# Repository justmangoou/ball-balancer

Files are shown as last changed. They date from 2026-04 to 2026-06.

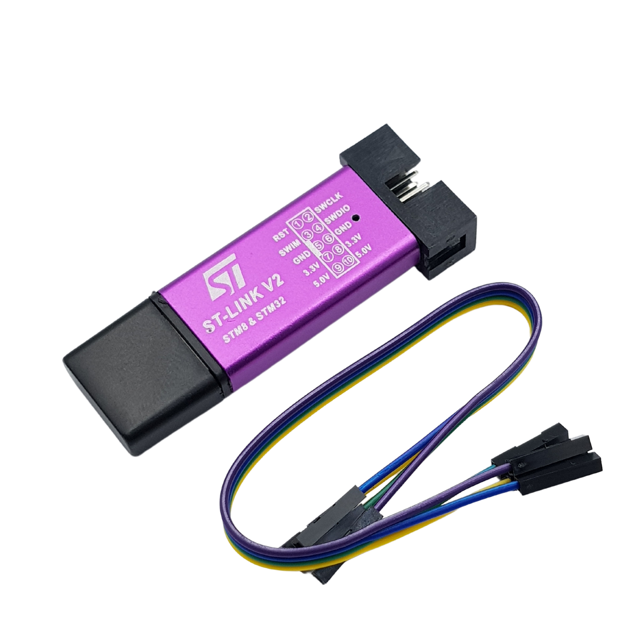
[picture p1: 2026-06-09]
report/assets/st-link.png

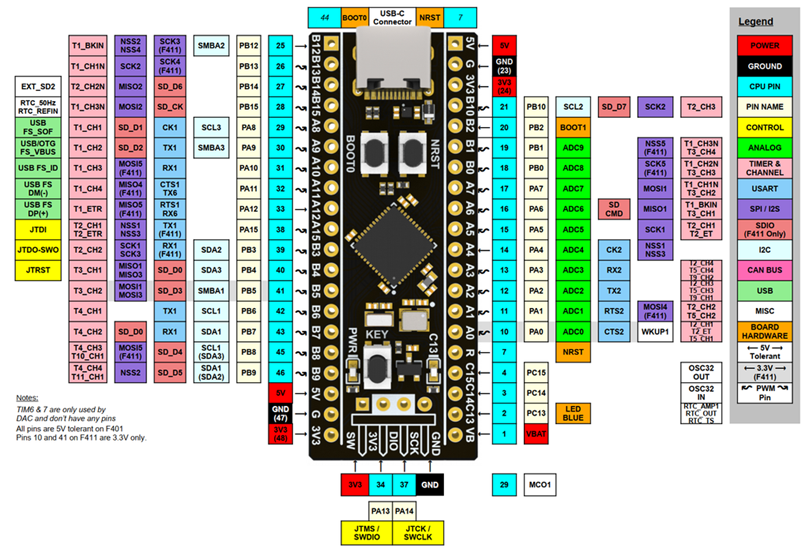
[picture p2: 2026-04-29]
report/assets/STM32F411CEU6-pinout.png

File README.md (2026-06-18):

# Ball Balancer

## Acknowledgements & Credits

This project is heavily inspired by and built upon the open-source work of **Aaed Musa** ([Ball Balancer on Instructables](https://www.instructables.com/Ball-Balancer/)). 

Python scripts to log data and graph visualizer are generated using Claude Sonnet 4.6.

## Major changes (compare to original work)
- Use STM32F4 "Blackpill" instead of Teensy 4.1.
- Use STM32 firmware development tools instead of Arduino (using Hardware timer, FPU, ...).
- Re-design R-joint so it does not slip (mismatch step when working).

## Development
### Pre-requisites
- Python 3.10 or higher (with `matplotlib`, `numpy` and `pyserial` libraries)
- STM32CubeMX
- STM32CubeCLT
- OpenOCD
- Clion (preferred)
- ST-Link V2

*It's also possible to use STM32CubeIDE, but CLion is recommended for better coding and debugging experience.*

### Firmware
All firmware code is located in the `firmware` directory. The project is configured for STM32F411CEU6 "Blackpill" microcontroller.

## Scipts
To log data to terminal only:
```bash
python loggger.py
```

To log data to terminal, draw graph ``x_err``, ``y_err``, ``x_out``, ``y_out`` and save to csv file:
```bash
python live_debugger.py
```

To see the graph of the logged data from csv file:
```bash
python log_viewer.py --file logs/xxxx-xx-xx_xx-xx-xx.csv
```

## PID Tuning Tracker
| Times | Time | Kp | Ki | Kd | 
| :---: | :---: | :---: | :---: | :---: |
| **1** | [2026-06-09_14-49-30](logs/2026-06-09_14-49-30.csv) | `6E-4f` | `6E-5f` | `10E-6f` |
| **2** | [2026-06-09_16-08-42](logs/2026-06-09_16-08-42.csv) | `1.3E-3f` | `7E-5f` | `2.3E-5f` |
| **3** | [2026-06-09_16-36-50](logs/2026-06-09_16-36-50.csv) | `1.1E-3f` | `5E-5f` | `2.3E-5f` |
| **4** | [2026-06-09_16-38-50](logs/2026-06-09_16-38-50.csv) | `1.1E-3f` | `5E-5f` (x) / `7E-5f` (y) | `2.3E-5f` |
| **5** | [2026-06-09_16-54-01](logs/2026-06-09_16-54-01.csv) | `1.1E-3f` | `5.5E-5f` (x) / `7.5E-5f` (y) | `2.3E-5f` |
| **6** | [2026-06-09_16-58-05](logs/2026-06-09_16-58-05.csv) | `1.1E-3f` | `6E-5f` (x) / `7.5E-5f` (y) | `2.3E-5f` |

### BOM
| ID | Name  | Quantity | Description |
| --- | --- | --- | --- |
| STM32F411CEU6 | STM32 BlackPill | 1 | Microcontroller |
|  | Resistive Touch Panel | 1 | 4 Pins  |
| 17HS4401S | Stepper 42x42mm | 3 | 1.5 - 2A |
| TMC2208 | Stepper Driver | 3 |  |
| LM2596 | Voltage Regulator | 1 | 4 - 35 VDC Input, 1 - 35 VDC Ouput (3A)  |
|  | Capacitor | 3 | 35V - 220uF |
|  | 24V power supply  | 1 | 24V - 5A |
|  | Terminal Connector | 1 | 15A - 12 Ports |
|  | FPC/FFC to DIP Adapter Board | 1 | 4 Pins |
|  | DC Jack | 1 |  |
|  | USB to TTL | 1 | |
|  | Male and female header pin | many |  |

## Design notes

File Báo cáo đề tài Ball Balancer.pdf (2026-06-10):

### ĐẠI HỌC QUỐC GIA HÀ NỘI

### TRƯỜNG ĐẠI HỌC CÔNG NGHỆ

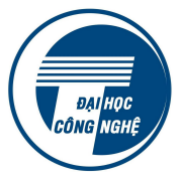
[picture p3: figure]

### BÁO CÁO MÔN HỌC

### THỰC HÀNH VÀ XÂY DỰNG ROBOT 2

### Đề tài: Robot cân bằng bóng trên mặt phẳng

Giảng viên hướng dẫn: | Đặng Anh Việt Nguyễn Quốc Bảo
Sinh viên thực hiện: | Nguyễn Hoàng Tuấn - 24022923 Đỗ Minh - 24022889
Lớp: | K69E-RE1
Lớp học phần | RBE2022 2

Hà Nội — 2026

## Mục lục

## Danh mục hình

Hình 3.8 Sơ đồ kết nối tổng thể giữa vi điều khiển, driver động cơ và các khối chức

Hình 5.1 Đồ thị biểu diễn sự thay đổi về đầu vào/ra của hai trục X/Y

Hình 5.2 Đồ thị biểu diễn sự thay đổi về đầu vào/ra của hai trục X/Y

## Danh mục bảng

Bảng 3.8 Sơ đồ kết nối các chân của driver TMC2208 với nguồn và động cơ bước . 20

## Danh mục ký hiệu và từ viết tắt

ADC | Analog-to-Digital Converter Bộ chuyển đổi tín hiệu tương tự sang tín hiệu số.
ARM | Advanced RISC Machine Kiến trúc vi xử lý dựa trên tập lệnh rút gọn (RISC).
DC | Direct Current Dòng điện một chiều.
DIP | Dual In-line Package (hoặc Dual In-line Pins) Kiểu chân linh kiện có hai hàng chân song song, khoảng cách tiêu chuẩn (thường là 2.54mm).
DWT | Data Watchpoint and Trace Khối ngoại vi thuộc lõi ARM hỗ trợ giám sát hệ thống và cung cấp bộ đếm chu kỳ xung nhịp.
FFC | Flexible Flat Cable Cáp dẹt mềm, dùng để kết nối dẫn điện giữa các bo mạch hoặc module thông qua đầu cắm chuyên dụng.
FPC | Flexible Printed Circuit Mạch in dẻo, có thể tích hợp linh kiện và đường mạch phức tạp trên nền vật liệu đàn hồi, dùng cho các kết nối nhỏ gọn.
FPU | Floating Point Unit Bộ xử lý số học dấu chấm động.
GPIO | General Purpose Input/Output Các chân vào/ra đa dụng của vi điều khiển.
IDE | Integrated Development Environment Môi trường phát triển tích hợp dùng để viết, biên dịch và quản lý mã nguồn.

NEMA | National Electrical Manufacturers Association Chuẩn kích thước mặt bích động cơ (ví dụ NEMA 17).
PID | Proportional–Integral–Derivative Thuật toán điều khiển phản hồi gồm ba thành phần Tỉ lệ (P), Tích phân (I) và Đạo hàm (D).
PWM | Pulse Width Modulation Kỹ thuật điều chế độ rộng xung dùng để kiểm soát mức cống suất trung bình.
RMS | Root Mean Square Giá trị hiệu dụng của tín hiệu (ví dụ điện áp/dòng), tương đương giá trị DC tạo ra cùng công suất trên tải.
ROM | Read-Only Memory Bộ nhớ chỉ đọc, dùng để lưu trữ chương trình.
RPS | Revolute–Prismatic–Spherical Chuỗi khớp quay–tịnh tiến–cầu trong cơ cấu robot song song.
SRAM | Static Random Access Memory Bộ nhớ truy cập ngẫu nhiên tĩnh, dùng để lưu dữ liệu tạm thời khi chạy chương trình.
SYSCLK | System clock Xung nhịp hệ thống của vi điều khiển.
TIM | Timer Bộ định thời: tạo mốc thời gian và xung nhịp để đếm, tạo ngắt định kỳ, đo độ rộng/tần số xung và tạo PWM.
UART | Universal Asynchronous Receiver/Transmitter Chuẩn truyền nhận dữ liệu nối tiếp bất đồng bộ.

## CHƯƠNG 1: GIỚI THIỆU

### 1.1. Bài toán

Hệ thống cân bằng bóng trên mặt phẳng là một bài toán điển hình trong lĩnh vực

điều khiển tự động, thường được dùng để minh họa điều khiển phản hồi và khả năng ổn

định của một hệ cơ điện tử.

Đây là một bài toán thách thức do hệ có nhiều yếu tố phi tuyến và không lý tưởng.

Chuyển động của bóng phụ thuộc vào góc nghiêng của mặt phẳng, ma sát và đặc tính bề

mặt. Ngoài ra, hệ chịu ảnh hưởng của độ trễ và nhiễu phát sinh từ phần cơ khí cũng như

từ quá trình đo lường. Những yếu tố này khiến hệ có xu hướng xuất hiện dao động hoặc

không đáp ứng được yêu cầu về biên độ và tốc độ nếu hệ thống không được thiết kế và

hiệu chỉnh phù hợp.

### 1.2. Mục tiêu và phạm vi của đề tài

Mục tiêu của đề tài là xây dựng một hệ thống có khả năng:

- Xác định vị trí quả bóng trên mặt phẳng: thu nhận và xử lý tín hiệu để xác

định tọa độ (x, y) của bóng.

- Điều khiển mặt phẳng để đưa bóng về vị trí đặt: xây dựng thuật toán điều

khiển nhằm điều chỉnh chuyển động của mặt phẳng để giảm sai lệch vị trí.

- Duy trì trạng thái cân bằng ổn định: hạn chế dao động, nhiễu và đảm bảo sai

số xác lập nhỏ quanh vị trí mong muốn.

Trong phạm vi đề tài, hệ thống được triển khai trong môi trường thí nghiệm với một

quả bi thép đơn và mặt phẳng kích thước cố định. Bài toán tập trung vào điều khiển vị

trí trong một vùng làm việc giới hạn trên mặt phẳng và đánh giá chất lượng điều khiển

thông qua các tiêu chí như: thời gian đáp ứng, độ dao động và sai số xác lập.

### 1.3. Cơ sở tham khảo

Đề tài tham khảo mô hình Ball Balancer của Aaed Musa được đăng trên nền tảng

Instructables: https://www.instructables.com/Ball-Balancer/.

Trong đề tài này, thiết kế cơ khí được kế thừa với kích thước và tỉ lệ được điều

chỉnh phù hợp với phần cứng. Sơ đồ kết nối mạch được dựa trên nguyên lý tương tự, với

một số thay đổi nhằm đảm bảo sự tương thích với linh kiện được sử dụng.

## CHƯƠNG 2: CƠ SỞ LÝ THUYẾT

### 2.1. Mô hình Robot 3-RPS

Robot 3RPS là một cơ cấu song song gồm 3 chân (3 nhánh) có chuỗi khớp theo thứ

tự: R (Revolute – khớp quay) ở đế, P (Prismatic – khớp tịnh tiến, thường là cơ cấu vít

me/đai ốc hoặc thanh trượt được dẫn động) và S (Spherical – khớp cầu) nối với bàn công

tác. Nhờ cấu trúc song song, 3RPS có độ cứng vững tốt, sai số tích lũy nhỏ và phù hợp

cho các bài toán điều khiển nghiêng mặt phẳng (tilt) như cân bằng bi.

Về bậc tự do, với bố trí đối xứng thường gặp, 3RPS tạo ra 3 bậc tự do của bàn công

tác (thường là 2 góc nghiêng roll/pitch và 1 tịnh tiến theo trục z). Khi điều khiển cân

bằng bi trên mặt phẳng, ta chủ yếu quan tâm đến hai góc nghiêng của bàn; còn độ cao z

thường được xem là hằng hoặc biến thiên nhỏ tùy theo thiết kế.

Để mô tả động học, đặt hệ tọa độ gốc {B} gắn với đế, hệ {P} gắn với bàn công tác.

Gọi Bi

là tọa độ các điểm gắn chân trên đế trong {B}, và Pi

là tọa độ các điểm gắn chân

trên bàn trong {P}, với i = 1..3. Tư thế của bàn được mô tả bởi ma trận quay R và vectơ

tịnh tiến p (từ {B} đến gốc {P}). Khi đó vectơ chân thứ i trong {B} là:

l

i = p + RPi − Bi

Chiều dài (hoặc hành trình hiệu dụng) của chân i là:

qi = ‖l
i

‖

Đây là dạng động học nghịch điển hình: cho tư thế mong muốn (R, p), ta tính được

q1

, q2

, q3

để sinh lệnh cho các cơ cấu tịnh tiến (xung bước/độ quay motor → dịch

chuyển). Ngược lại, động học thuận (từ qi
suy ra (R, p)) thường phức tạp hơn và hay được giải bằng phương pháp số; trong bài toán cân bằng, hệ thống có thể dùng cảm biến

(màn cảm ứng) để phản hồi trực tiếp trạng thái bi nên không nhất thiết phải giải động

học thuận chính xác ở mọi thời điểm.

### 2.2. Màn cảm ứng điện trở

Màn cảm ứng điện trở hoạt động dựa trên hai lớp dẫn điện được ngăn cách bởi một

lớp cách điện mỏng. Khi có lực tác động lên bề mặt, hai lớp này tiếp xúc tại điểm chạm,

tạo thành một cầu điện trở. Bằng cách đo điện áp tại điểm tiếp xúc, hệ thống có thể xác

định tọa độ theo hai trục X và Y.

Ưu điểm của loại màn này là chi phí thấp và có thể sử dụng với nhiều vật liệu tiếp

xúc. Tuy nhiên, nhược điểm là độ bền không cao, độ nhạy kém hơn so với màn cảm ứng

điện dung và không hỗ trợ đa điểm hiệu quả.

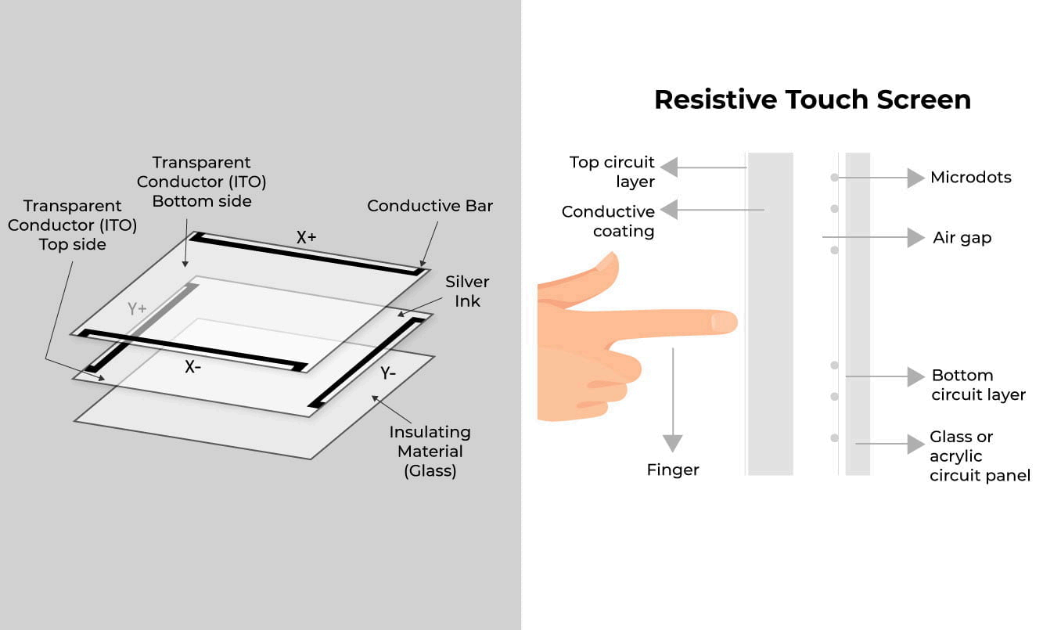
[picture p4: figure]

Hình 2.1: Cấu tạo của màn cảm ứng điện trở

### 2.3. Cơ sở phát xung động cơ bước

Động cơ bước được điều khiển thông qua hai tín hiệu STEP và DIR. Mỗi xung

STEP tương ứng với một bước dịch chuyển của động cơ, trong khi tín hiệu DIR xác định

chiều quay.

Trong hệ thống này, vận tốc được biểu diễn dưới dạng số thực và được tích lũy

theo từng chu kỳ timer. Khi giá trị tích lũy đạt ngưỡng xác định, hệ thống phát một xung

STEP và cập nhật vị trí hiện tại của động cơ. Phương pháp này cho phép điều khiển vận

tốc mượt mà trong khi vẫn duy trì chu kỳ timer cố định.

### 2.4. Thuật toán điều khiển PID

Thuật toán điều khiển Proportional–Integral–Derivative (PID) là một phương pháp

điều khiển phản hồi được sử dụng phổ biến trong các hệ thống. Trong đó tín hiệu điều

khiển được xác định dựa trên sai lệch giữa giá trị đặt và giá trị đo được của hệ thống. Cách

tiếp cận này cho phép hệ thống liên tục điều chỉnh để đạt được trạng thái mong muốn.

Bộ điều khiển PID bao gồm ba thành phần chính:

- Thành phần tỉ lệ (P): tạo ra tín hiệu điều khiển tỉ lệ với sai số tức thời, giúp hệ

thống phản ứng nhanh với sự thay đổi.

- Thành phần tích phân (I): tích lũy sai số theo thời gian, nhằm loại bỏ sai số xác

lập và cải thiện độ chính xác lâu dài.

- Thành phần đạo hàm (D): phản ánh tốc độ biến thiên của sai số, từ đó hỗ trợ

giảm dao động và cải thiện tính ổn định của hệ thống.

Biểu thức tổng quát của bộ điều khiển trong miền thời gian được viết như sau:

u(t) = Kp

e(t) + Ki ∫ e(t) dt + Kd

de(t)
dt

Trong đó:
- e(t) là sai lệch giữa giá trị mong muốn và giá trị đo được
- Kp

, Ki

, Kd

là các hệ số điều khiển.

Các tham số này cần được hiệu chỉnh phù hợp để đảm bảo hệ thống đạt được các đặc tính

đáp ứng mong muốn như thời gian xác lập ngắn, độ vượt quá nhỏ và sai số xác lập thấp.

Trong quá trình triển khai thực tế, hiện tượng integral windup có thể xảy ra khi

tín hiệu điều khiển bị giới hạn bởi các ràng buộc vật lý, trong khi thành phần tích phân

vẫn tiếp tục tích lũy sai số, dẫn đến đáp ứng vượt mức khi hệ thống trở lại vùng hoạt

động bình thường. Để khắc phục, có thể áp dụng một số kỹ thuật như giới hạn giá trị tích

phân (anti-windup clamping), tạm dừng tích lũy khi đầu ra bị bão hòa, hoặc hiệu chỉnh

lại thành phần tích phân dựa trên tín hiệu điều khiển thực tế.

## CHƯƠNG 3: THIẾT KẾ VÀ TRIỂN KHAI HỆ THỐNG

### 3.1. Thiết kế tổng thể

Hệ thống được thiết kế theo mô hình điều khiển vòng kín, trong đó vị trí của quả

bóng được đo liên tục và sử dụng làm tín hiệu phản hồi để điều chỉnh trạng thái của

hệ thống.

Về mặt chức năng, hệ thống bao gồm ba khối chính:

- Khối cảm biến: sử dụng màn hình cảm ứng điện trở để xác định tọa độ (x, y)

của quả bóng.
- Khối xử lý: vi điều khiển thực hiện nhiệm vụ thu nhận dữ liệu và tính toán tín

hiệu điều khiển.

- Khối chấp hành: bao gồm driver và các động cơ bước để điều chỉnh góc nghiêng

của mặt phẳng.

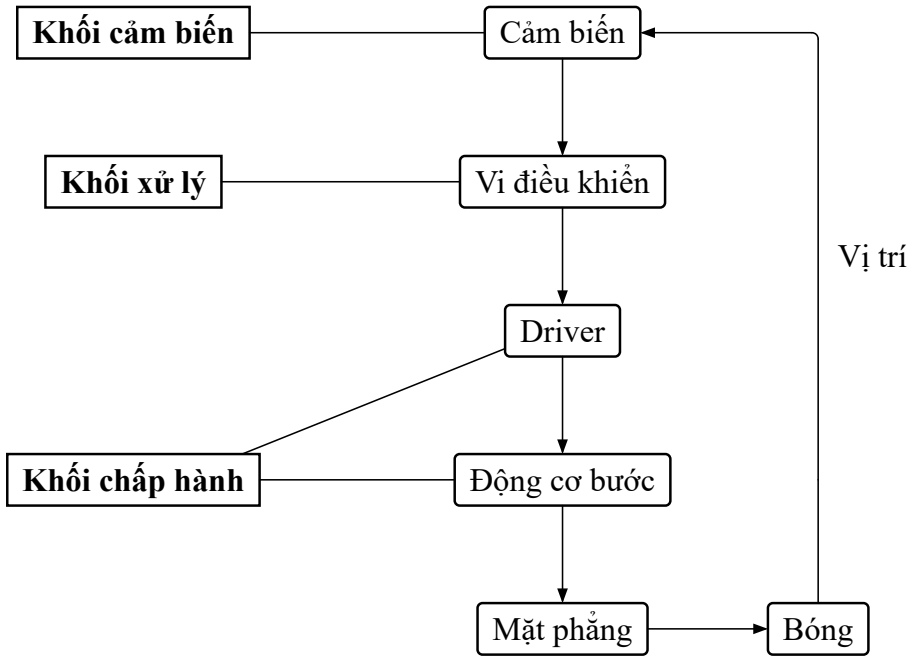
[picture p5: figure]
Vị trí; Cảm biến; Vi điều khiển; Driver; Động cơ bước; Mặt phẳng; Bóng; Khối cảm biến; Khối xử lý; Khối chấp hành

Hình 3.1: Sơ đồ khối tổng thể của hệ thống

Nguyên lý hoạt động của hệ thống như sau: tín hiệu vị trí từ cảm biến được đưa về bộ

điều khiển để xác định sai lệch so với vị trí đặt. Tín hiệu điều khiển sau đó được gửi tới

các động cơ bước nhằm điều chỉnh góc nghiêng của mặt phẳng, từ đó chi phối chuyển

động của quả bóng. Quá trình này được lặp lại liên tục theo thời gian thực để đảm bảo

hệ thống duy trì trạng thái cân bằng ổn định.

### 3.2. Thiết kế phần cứng

### 3.2.1. Danh sách linh kiện

### 3.2.1.1. Vi điều khiển STM32F411CEU6

STM32F411CEU6 (Blackpill) là vi điều khiển thuộc dòng STM32F4 của STMi-

croelectronics, sử dụng nhân ARM Cortex-M4 tích hợp Floating Point Unit (FPU), cho phép xử lý hiệu quả các phép toán số thực, phù hợp với các hệ thống điều khiển yêu cầu

hiệu suất cao.

Bảng 3.1: Thông số kỹ thuật STM32F411CEU6

Nhân | ARM 32-bit Cortex-M4
Tốc độ xung nhịp tối đa | 100 MHz
Bộ nhớ Flash (ROM) | 512 KB
Bộ nhớ SRAM | 128 KB
GPIO | 34 chân I/O
ADC | 12-bit, 9 kênh
Kích thước | 21 x 53 mm

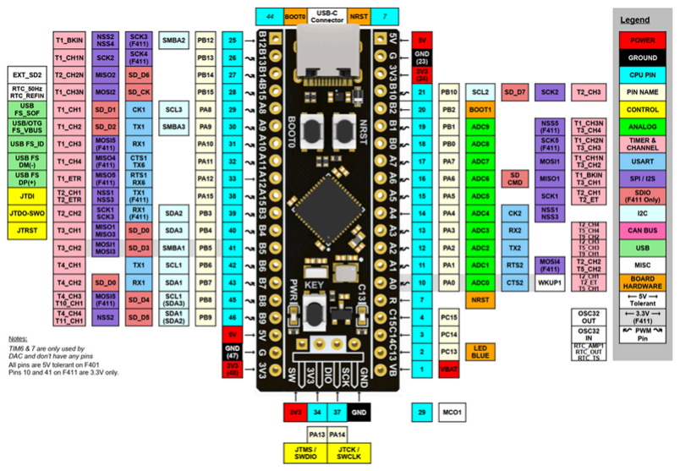
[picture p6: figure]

Hình 3.2: Sơ đồ chân của STM32F411CEU6 (Blackpill)

### 3.2.1.2. Màn cảm ứng điện trở

Màn hình cảm ứng điện trở được sử dụng để thu nhận thông tin vị trí tiếp xúc

trên bề mặt. Với cấu trúc 4 dây điện trở, thiết bị có khả năng xác định vị trí chạm với

độ chính xác tương đối cao và ổn định. Nhờ kích thước vùng hoạt động lớn và cấu tạo

đơn giản, loại màn hình này phù hợp với các ứng dụng yêu cầu xác định vị trí trên mặt

phẳng với chi phí thấp. Nguyên lý hoạt động được trình bày tại Mục 2.2.

Bảng 3.2: Thông số kỹ thuật màn cảm ứng điện trở

Kích thước | 9 inch
Vùng hoạt động | 210 × 126 mm
Vật liệu bề mặt | Màng phim + kính

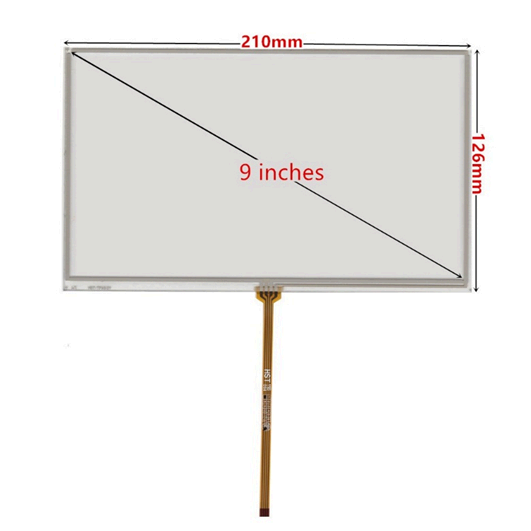
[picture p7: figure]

Hình 3.3: Màn hình cảm ứng điện trở 9″

### 3.2.1.3. Driver TMC2208

Driver TMC2208 là bộ điều khiển động cơ bước tích hợp các công nghệ

StealthChop2™︎ và SpreadCycle™︎ của Trinamic. Các công nghệ này giúp hạn chế tiếng

ồn, đồng thời đảm bảo chuyển động mượt với độ chính xác cao thông qua cơ chế vi

bước. Đồng thời, driver tối ưu hiệu suất năng lượng và giảm sinh nhiệt trong quá trình

vận hành lâu dài. Dòng điện cấp cho động cơ có thể được điều chỉnh thông qua điện áp

tham chiếu (Vref) hoặc giao tiếp UART, cho phép tự cấu hình tùy theo yêu cầu hệ thống.

Bảng 3.3: Thông số kỹ thuật driver TMC2208

Điện áp động cơ (VM) | 4.75V đến 36V
Điện áp logic (VIO) | 3V đến 5V
Dòng điện | 1.2A RMS (Tối đa ∼ 2.0A với tản nhiệt)
Độ phân giải vi bước | Tối đa 1 / 256 bước
Kích thước | 20.2 × 15.4 mm

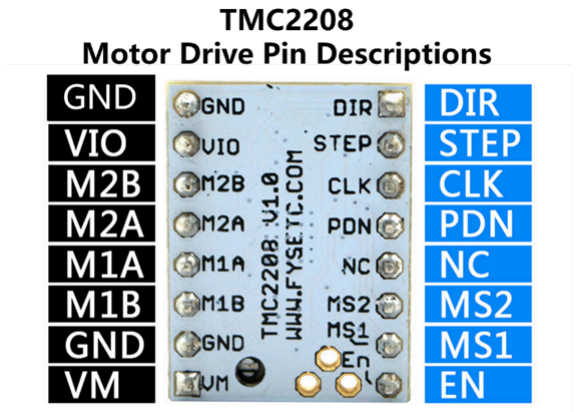
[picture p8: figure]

Hình 3.4: Sơ đồ chân cắm mạch điều khiển động cơ bước TMC2208

### 3.2.1.4. Động cơ bước 17HS4401S

Động cơ bước 17HS4401S (chuẩn NEMA 17) là động cơ bước hai pha (bipolar)

được sử dụng phổ biến trong các hệ thống yêu cầu độ chính xác và độ ổn định cao. Động

cơ có góc bước cơ bản nhỏ và mô-men giữ tương đối lớn.

Bảng 3.4: Thông số kỹ thuật động cơ bước 17HS4401S

Góc bước cơ bản | 1.8° ± 0.09°
Kích thước mặt bích | 42.3 × 42.3 mm
Dòng điện định mức | 1.5A / pha
Mô-men xoắn giữ | 40N ⋅ cm
Khối lượng | ∼ 300 g

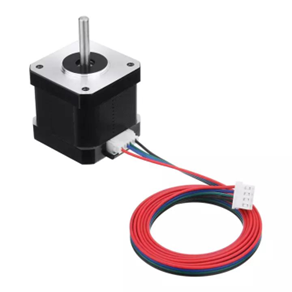
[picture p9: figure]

Hình 3.5: Động cơ bước 17HS4401S

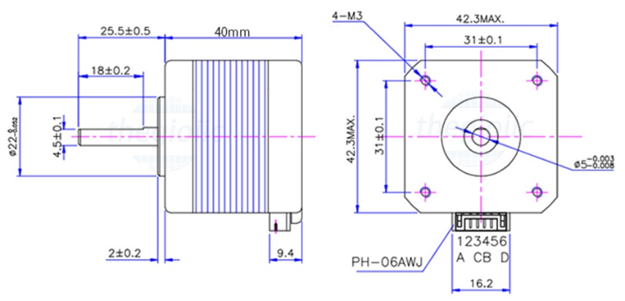
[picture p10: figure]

Hình 3.6: Bản vẽ kỹ thuật động cơ bước 17HS4401S

### 3.2.1.5. Module hạ áp LM2596

Module hạ áp DC-DC LM2596 (tích hợp vôn kế) là bộ chuyển đổi điện áp một

chiều có khả năng hạ điện áp đầu vào xuống mức thấp hơn, hoạt động theo nguyên lý

chuyển mạch tần số cao, cho hiệu suất chuyển đổi cao. Module được tích hợp màn hình

LED và vi điều khiển đo điện áp, giúp giám sát trực tiếp điện áp đầu vào/đầu ra trong

quá trình vận hành với độ chính xác khoảng ±0.05V . Điện áp đầu ra có thể thay đổi

thông qua việc điều chỉnh biến trở tích hợp trên module.

Bảng 3.5: Thông số kỹ thuật module hạ áp DC-DC LM2596

Điện áp đầu vào Vin | 4.0V đến 40V (Vôn kế hoạt động khi Vin > 4.5V )
Điện áp đầu ra Vout | 1.25V đến 37V (Điều chỉnh bằng biến trở)
Dòng điện đầu ra | 2.0A RMS (Tối đa ∼ 3.0A với tản nhiệt)
Công suất đầu ra tối đa | 20W Tản nhiệt nếu P > 15W
Hiệu suất chuyển đổi | ∼ 88%
Kích thước | 65 × 39.3 mm

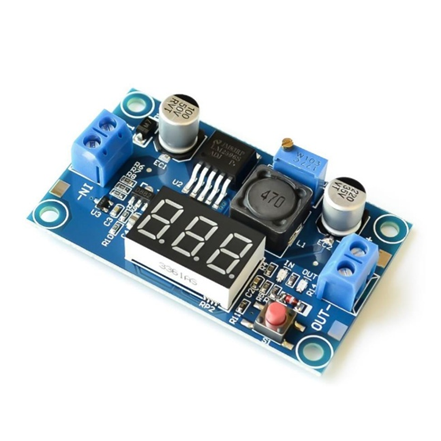
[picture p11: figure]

Hình 3.7: Module hạ áp DC-DC LM2596 (tích hợp vôn kế)

### 3.2.1.6. Linh kiện phụ trợ

Bảng 3.6: Danh sách các linh kiện phụ trợ

Tụ điện | 220μF – 35V
Nguồn DC | 24V – 5A
Cầu đầu điện | 6 cổng - 15A

Mạch chuyển FPC/ FFC sang DIP

### 3.2.2. Sơ đồ nối mạch

Sơ đồ nối mạch thể hiện cách liên kết tổng thể giữa các thành phần chính trong hệ

thống, bao gồm vi điều khiển, cảm biến, driver động cơ và nguồn cấp. Sơ đồ này giúp

minh họa trực quan cấu trúc phần cứng và luồng kết nối giữa các khối chức năng.

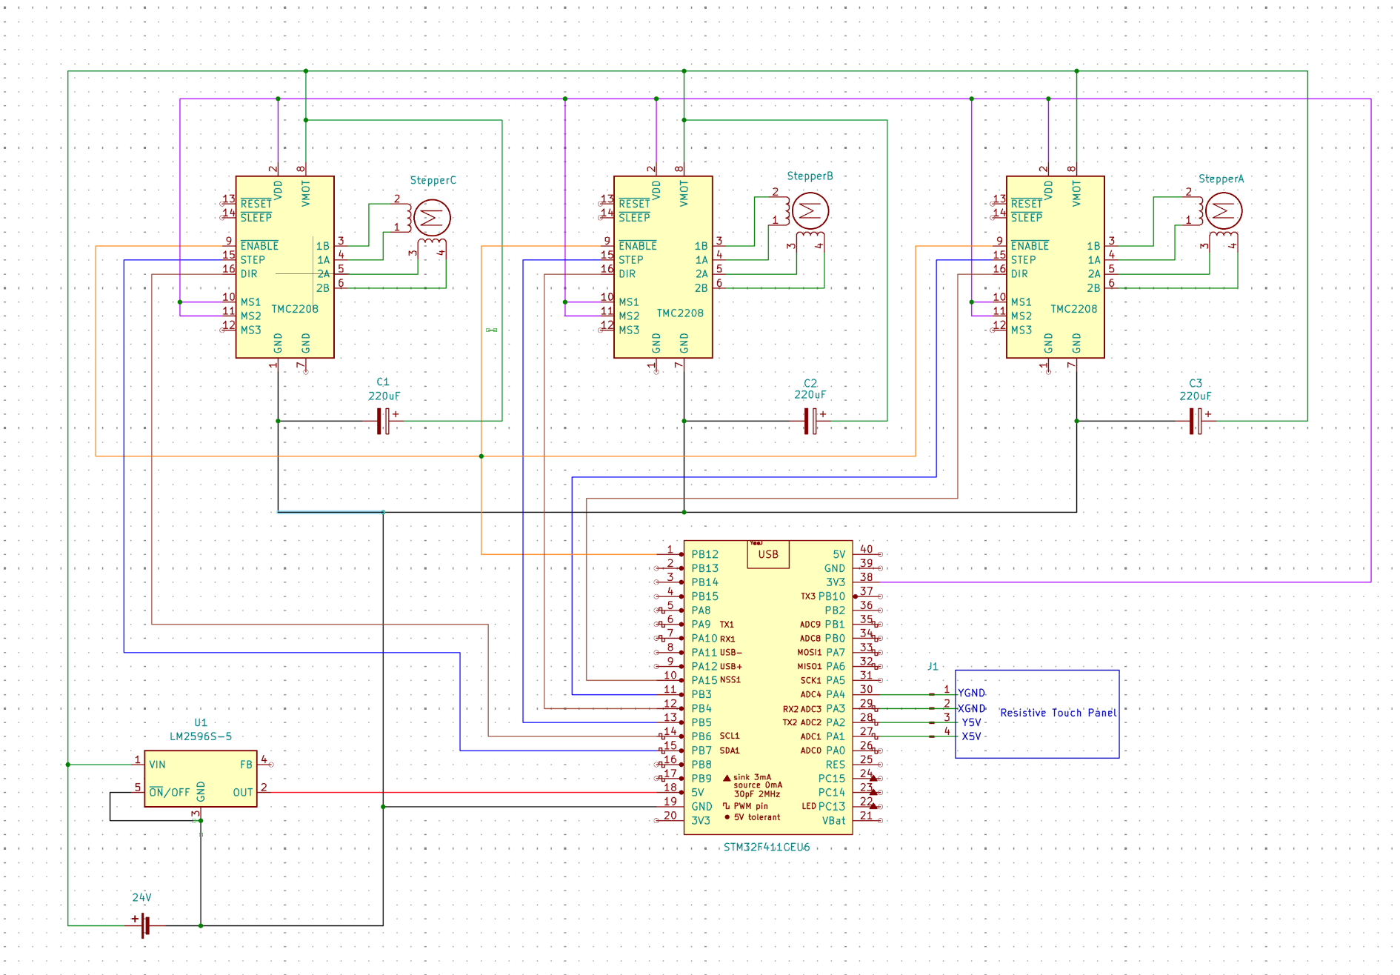
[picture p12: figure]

Hình 3.8: Sơ đồ kết nối tổng thể giữa vi điều khiển, driver động cơ và các khối chức năng

Một số kết nối phụ trợ được lược bỏ để đơn giản hóa sơ đồ:

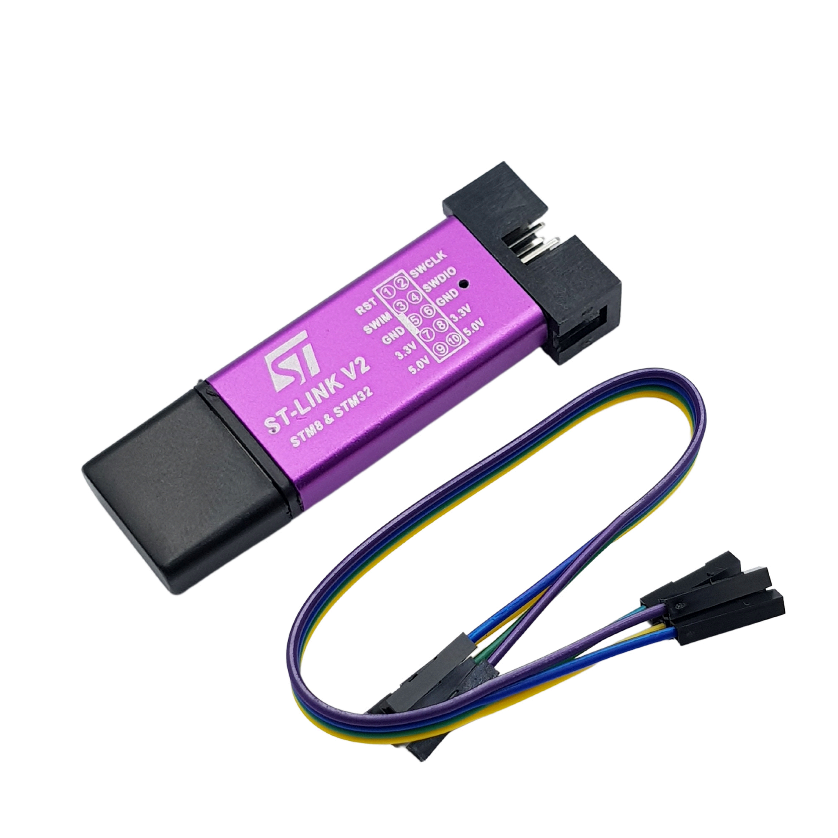
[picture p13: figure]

Hình 3.9: Mạch nạp và gỡ lỗi ST-Link V2

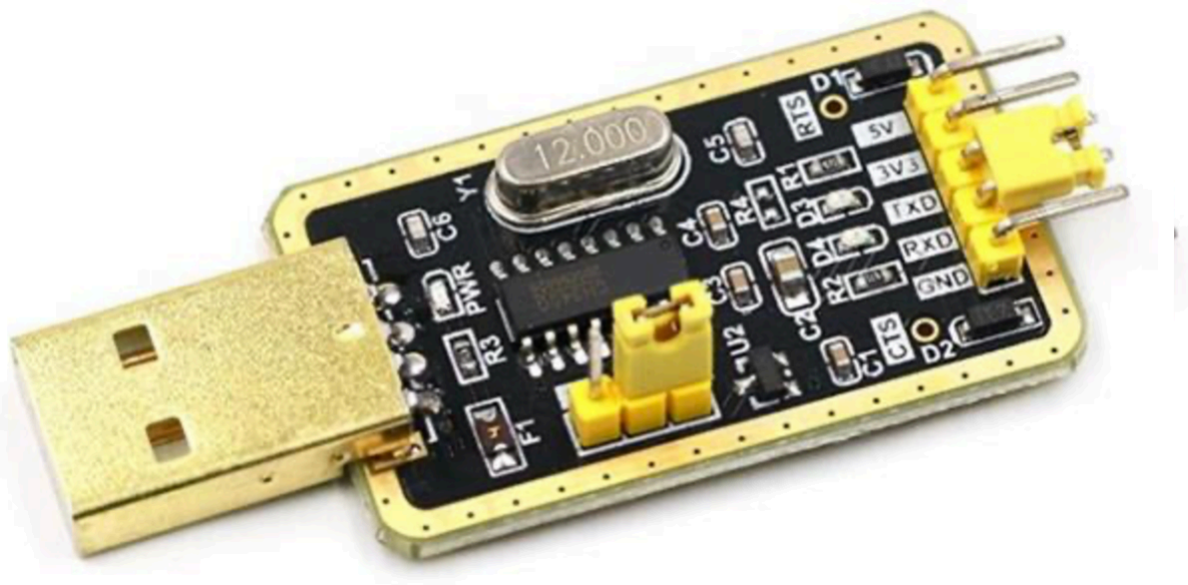
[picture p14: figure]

Hình 3.10: Mạch chuyển USB sang TTL/COM (UART)

### 3.2.3. Sơ đồ chân nối

Bảng dưới đây trình bày chi tiết kết nối giữa các chân của linh kiện và chân của vi

điều khiển, bao gồm cả cấu hình I/O tương ứng.

Bảng 3.7: Sơ đồ chân nối với vi điều khiển

Linh kiện | Chân linh kiện | Chân vi điều khiển | Cấu hình I/O
Màn cảm ứng | X+ | PA1 | ADC / GPIO Out
Màn cảm ứng | Y+ | PA2 | ADC / GPIO Out
Màn cảm ứng | X- | PA3 | ADC / GPIO In
Màn cảm ứng | Y- | PA4 | ADC / GPIO In
TMC2208 A | STEP | PA15 | GPIO Out
TMC2208 A | DIR | PB3 | GPIO Out
TMC2208 A | EN | PB12 | GPIO Out
TMC2208 B | STEP | PB5 | GPIO Out
TMC2208 B | DIR | PB4 | GPIO Out
TMC2208 B | EN | PB12 | GPIO Out
TMC2208 C | STEP | PB7 | GPIO Out
TMC2208 C | DIR | PB6 | GPIO Out
TMC2208 C | EN | PB12 | GPIO Out
LM2596 | OUT+ | 3V3 | -
LM2596 | OUT- | GND | -

Trong đó, các chân điều khiển của driver TMC2208 (STEP, DIR, EN) được kết nối

trực tiếp với các chân GPIO của vi điều khiển, cho phép điều khiển độc lập từng động

cơ. Các chân EN được nối chung để có thể bật/tắt đồng thời toàn bộ driver.

Đối với màn cảm ứng điện trở, các chân được cấu hình linh hoạt giữa chế độ GPIO

và ADC để thực hiện việc đo tọa độ, theo nguyên lý hoạt động đã trình bày tại Mục 2.2.

Bảng 3.8: Sơ đồ kết nối các chân của driver TMC2208 với nguồn và động cơ bước

Chân driver | Kết nối / chức năng
VM | Nguồn động cơ (DC 24V)
VIO | Nguồn logic (3.3V)
GND | Đất chung
M1A | Cuộn 1 - Động cơ bước
M1B | Cuộn 1 - Động cơ bước
M2A | Cuộn 2 - Động cơ bước
M2B | Cuộn 2 - Động cơ bước
MS1 | 3V3 - Cấu hình vi bước
MS2 | 3V3 - Cấu hình vi bước

Việc thiết lập các chân MS1 và MS2 ở mức cao (3.3V) cấu hình driver hoạt động ở

chế độ vi bước 1/16. Chế độ này giúp cải thiện độ mượt của chuyển động, tăng độ phân

giải điều khiển và giảm rung động cũng như tiếng ồn của động cơ bước.

Trong thiết kế này, giao tiếp UART của driver không được sử dụng. Thay vào đó,

các tham số hoạt động được cấu hình thông qua các chân phần cứng (MS1, MS2). Cách

tiếp cận này giúp giảm độ phức tạp của hệ thống, đơn giản hóa việc lập trình và giảm

yêu cầu về tài nguyên vi điều khiển, đồng thời vẫn đáp ứng đủ yêu cầu điều khiển của

bài toán.

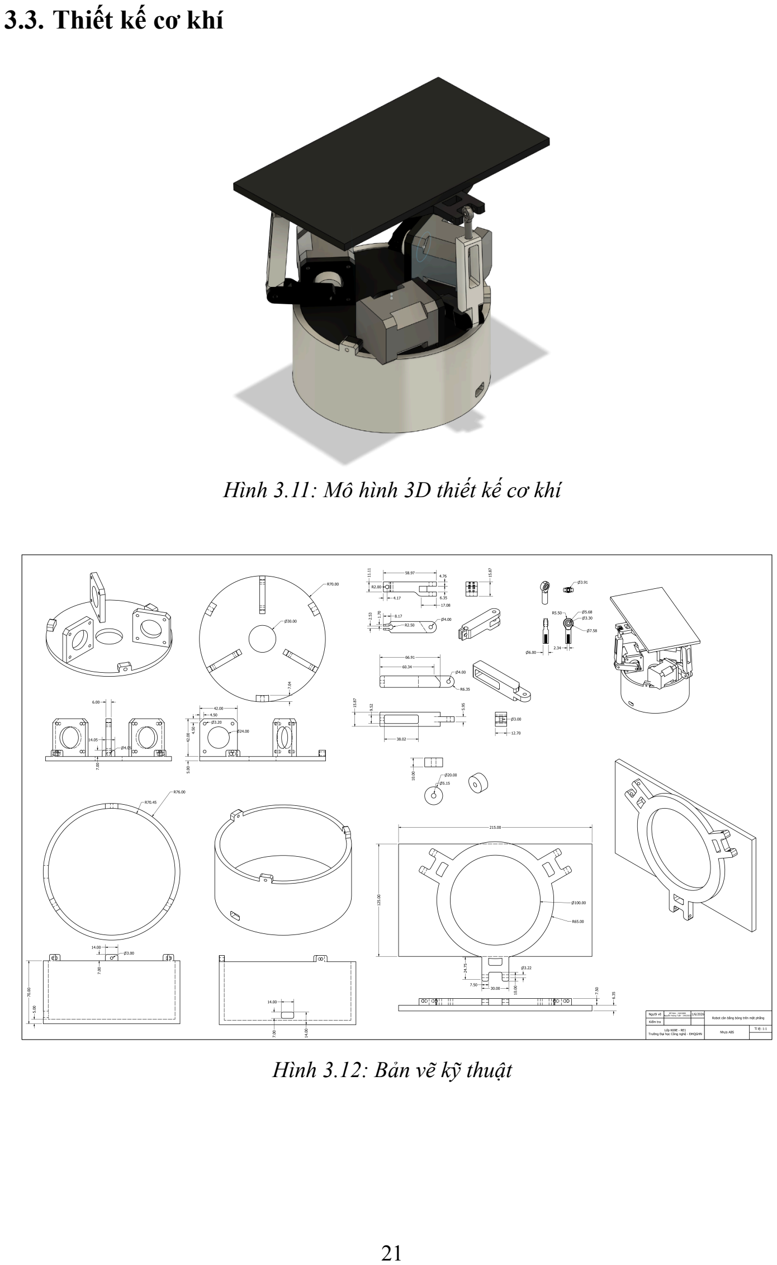
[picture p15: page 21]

### 3.3. Thiết kế cơ khí

Hình 3.11: Mô hình 3D thiết kế cơ khí

Hình 3.12: Bản vẽ kỹ thuật

### 3.4. Kiến trúc phần mềm

### 3.4.1. Công cụ phát triển

Trong quá trình phát triển hệ thống, các công cụ phần mềm sau được sử dụng:

- STM32CubeMX: (https://www.st.com/en/development-tools/stm32cubemx.html) dùng để cấu hình vi điều khiển, thiết lập clock, GPIO, ADC

và các ngoại vi cần thiết, đồng thời sinh mã khởi tạo ban đầu.

- OpenOCD (http://openocd.org/) và STM32CubeProgrammer: (https://www.st.com/en/development-tools/stm32cubeprog.html) được sử dụng để nạp chương trình

xuống vi điều khiển và thực hiện debug trong quá trình phát triển.

- CLion: (https://www.jetbrains.com/clion/) môi trường phát triển tích hợp (IDE) dùng để viết, quản lý và debug mã

nguồn chương trình.

- CMake: (https://cmake.org/) công cụ tạo hệ thống biên dịch, dùng để cấu hình và sinh các tệp phục

vụ quá trình biên dịch và liên kết chương trình (ví dụ: Makefile, Ninja).

### 3.4.2. Cấu hình xung nhịp hệ thống

Hệ thống sử dụng nguồn xung nhịp ngoài HSE với tần số 25 MHz. Thông qua bộ

nhân tần PLL với các tham số cấu hình M = 25, N = 200 và P = 2, vi điều khiển đạt

xung nhịp hệ thống (SYSCLK) 100 MHz.

Các tham số này được lựa chọn nhằm đảm bảo các điều kiện hoạt động tối ưu của

PLL: hệ số M = 25 đưa tần số đầu vào của PLL về 1 MHz (thuộc trong dải khuyến

nghị), hệ số N = 200 tạo tần số VCO đạt 200 MHz (thuộc dải hoạt động cho phép), và

hệ số P = 2 chia tần số này xuống 100 MHz, tương ứng với tần số tối đa của hệ thống.

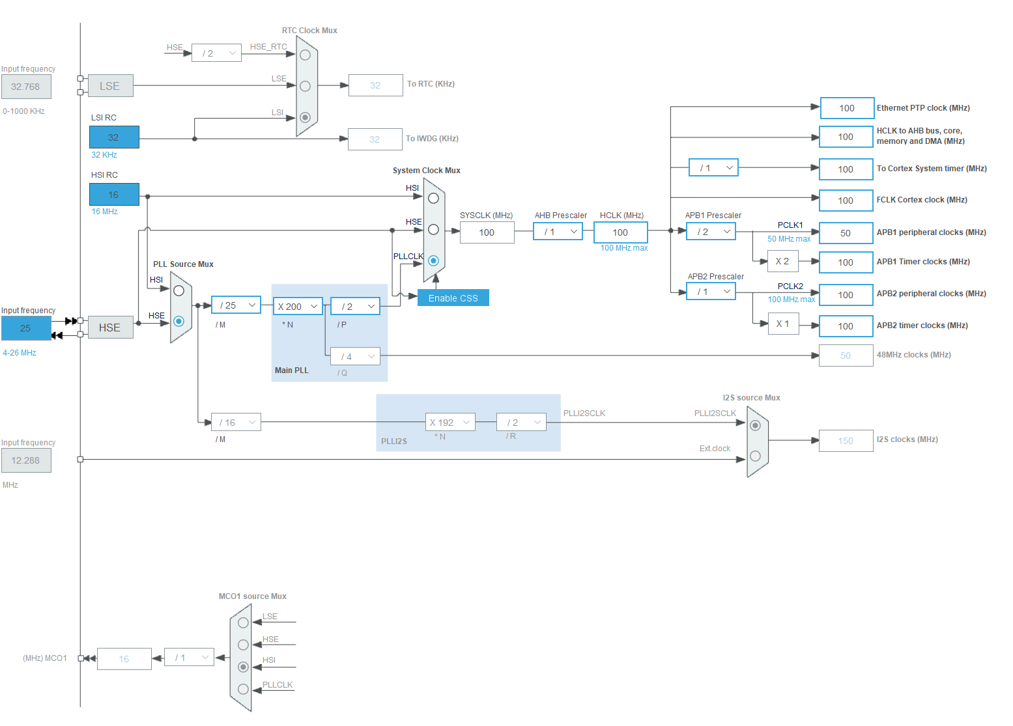
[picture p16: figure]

Hình 3.13: Cấu hình xung nhịp hệ thống

Cấu hình này đảm bảo hiệu năng xử lý đủ cao cho các tác vụ thời gian thực, bao gồm

thu thập dữ liệu cảm biến, xử lý thuật toán điều khiển và phát xung điều khiển động cơ

với độ chính xác cao:

- HCLK (AHB bus): 100 MHz.
- PCLK1 (APB1): 50 MHz (Timer đạt 100 MHz).
- PCLK2 (APB2): 100 MHz.

Ngoài ra, bộ đếm chu kỳ DWT (Data Watchpoint and Trace) được sử dụng để xây dựng

các hàm trễ chính xác ở mức micro giây (μs), hỗ trợ đồng bộ hóa và điều khiển thời gian

trong hệ thống.

### 3.4.3. Thiết lập Timer

### 3.4.3.1. Timer điều khiển (TIM5)

Timer TIM5 đảm nhiệm làm nhiệm vụ điều khiển chính cho việc đọc cảm biến và

cập nhật thuật toán điều khiển.

Cấu hình:

- Prescaler: PSC = 99
- Auto-reload: ARR = 4999

f =

100 Mhz
(PSC + 1)(ARR + 1)

=

100 × 10

6
100 × 5000

= 200Hz

Tương ứng với chu kỳ 5ms.

### 3.4.3.2. Timer chấp hành (TIM9)

Timer TIM9 đảm nhiệm làm nhiệm vụ thực hiện xung PWM điều khiển động cơ

bước.

Cấu hình:

- Prescaler: PSC = 99
- Auto-reload: ARR = 24

f =

100 Mhz
(PSC + 1)(ARR + 1)

=

100 × 10

6
100 × 25

= 40kHz

Tương ứng với chu kỳ 25μs.

## CHƯƠNG 4: THUẬT TOÁN ĐIỀU KHIỂN

### 4.1. Xử lý tín hiệu cảm biến của màn cảm ứng điện trở

Mục tiêu của khối cảm biến là chuyển đổi tín hiệu tương tự từ màn cảm ứng điện

trở thành tọa độ (x,y) ổn định, có thể sử dụng trực tiếp làm tín hiệu phản hồi. Quá trình

đọc cảm biến được thực hiện định kỳ qua hàm ngắt TIM5 với chu kỳ 5ms.

### 4.1.1. Quy trình đọc x, y

Dựa theo nguyên lý hoạt động của màn cảm ứng điện trở tại Mục 2.2, việc xác định

tọa độ được thực hiện qua hai bước:

- Đo x: Thiết lập chân X⁺ ở mức cao và chân X⁻ ở mức thấp, cấu hình chân Y

+ và

Y

− ở chế độ analog, sau đó đọc điện áp tại kênh tương ứng Y

+ thông qua ADC.

- Đo y: Tương tự, thiết lập 2 chân Y

+, Y

− và đọc điện áp tại chân X⁺.

Sau khi thiết lập, hệ thống đợi 20μs trước khi lấy mẫu để đảm bảo điện áp trên màn cảm

ứng đạt trạng thái ổn định.

### 4.1.2. Lọc nhiễu bằng giá trị trung vị

Hệ thống lấy mẫu nhiều lần cho mỗi trục và sử dụng giá trị trung vị để làm kết quả

cuối cùng. Phương pháp này giúp giảm ảnh hưởng của các mẫu nhiễu hoặc do sai số

ngẫu nhiên.

Cụ thể, với số lượng lấy mẫu là 5 theo trục x: {x1
, x2

, x3

, x4

, x5}, các giá trị này
được sắp xếp theo thứ tự tăng dần và phần tử trung vị (x3
) sẽ được chọn làm xraw. Tương

tự với trục y (yraw).

### 4.1.3. Ước lượng lực nhấn (pressure) và kiểm tra hợp lệ

Ngoài tọa độ (x, y), hệ thống ước lượng thêm một đại lượng áp lực z nhằm loại bỏ

các lần chạm không ổn định dựa theo nguyên lý tại Mục 2.2. Hai giá trị z1
, z2
được đo
từ hai kênh ADC và được sử dụng để xây dựng một chỉ số áp lực theo dạng:

z = xraw ⋅

z2 − z1
z1

Trong phạm vi đề tài, đại lượng này không cần biểu diễn chính xác theo đơn vị vật lý,

mục đích chính là cung cấp một giải pháp nhằm phân biệt giữa trạng thái chạm thật (khi

có lực tác động đủ mạnh và ổn định) và chạm giả (nhiễu, không chạm hoặc chạm nhẹ

không ổn định).

Trong thiết kế hiện tại, một mẫu đo hợp lệ khi thỏa mãn các điều kiện sau:

- z ∈ [10, 4000]
- xraw và yraw < 4000

### 4.1.4. Chuẩn hoá về phần trăm lệch tâm

Tọa độ thô (xraw, yraw) không phản ánh trực tiếp vị trí lệch tâm của quả bóng trên bề

mặt phẳng, do đó cần chuyển sang một hệ quy chiếu phù hợp để biểu diễn vị trí của bóng.

Trong thiết kế này, hệ quy chiếu được chọn là phần trăm lệch tâm so với tâm bàn,

với vị trí trung tâm (0, 0) và giá trị dương/âm tương ứng với lệch theo hai chiều trục.

Tọa độ thô từ thang ADC 12-bit (0, 4096) được chuyển theo ngưỡng hiệu chuẩn (Xmin,

Xmax, Ymin, Ymax) sang phần trăm lệch tâm:

xpct, ypct ∈ [−100, 100]

Các ngưỡng Xmin, Xmax, Ymin, Ymax được xác định thông qua quá trình hiệu chuẩn thực

nghiệm. Cụ thể, hệ thống ghi nhận giá trị ADC khi điểm chạm được đưa tới các vị trí biên

của bề mặt cảm ứng tại 4 góc, từ đó xác định giá trị nhỏ nhất và lớn nhất theo từng trục.

### 4.1.5. Mất tín hiệu

Nếu tín hiệu từ cảm biến không hợp lệ (ví dụ: không phát hiện tiếp xúc, tiếp xúc

không ổn định hoặc nhiễu vượt ngưỡng) vượt quá ngưỡng 20 chu kỳ (tương đương 100

ms), hệ thống sẽ xác nhận mất tín hiệu, chuyển sang trạng thái “không tìm thấy” và đặt

các giá trị phản hồi về 0 nhằm tránh sử dụng dữ liệu không đáng tin cậy trong điều khiển.

### 4.2. Thuật toán điều khiển PID

Sau khi xác định được vị trí chuẩn hóa của quả bóng (xpct, ypct), hệ thống dùng hai

bộ điều khiển PID độc lập cho hai trục x và y để tính giá trị điều khiển tương ứng với độ

nghiêng của mặt phẳng. Nguyên lý tổng quát của thuật toán được trình bày trong Mục 2.4.

Thuật toán được thực thi trong cùng một hàm ngắt TIM5 với chu kỳ 5ms, do đó

mỗi bước lấy mẫu có Δt = 5ms.

Trong phạm vi của báo cáo, điểm đặt (setpoint) của thuật toán PID được chọn là 0

(tương ứng với tâm của mặt phẳng).

### 4.2.1. PID rời rạc theo chu kỳ

Với mỗi trục, sai số tại thời điểm rời rạc k được xác định:

e[k] = r[k] − y[k]

Trong đó:
- r[k] là giá trị đặt
- y[k] là giá trị đo được chuẩn hoá.

Thành phần tích phân được tính theo quy tắc hình thang (Trapezoidal rule):

I[k] = I[k − 1] +

e[k] + e[k − 1]
2

⋅ Δt

Để tránh integral windup, I[k] được giới hạn trong một khoảng phụ thuộc vào hệ số Ki :

I[k] ∈ [−

Imax
Ki

,

Imax
Ki

]

Trong đó Imax là giá trị giới hạn tích phân được xác định dựa trên đặc tính của hệ thống

và yêu cầu đáp ứng.

Thành phần vi phân được tính xấp xỉ qua sai phân và áp dụng bộ lọc thông thấp bậc

nhất nhằm giảm nhiễu:

D[k] = 0.1 ⋅ (e[k] − e[k − 1]) dt + 0.9 ⋅ D[k − 1]

Tổng hợp lại, tín hiệu điều khiển được xác định bởi:

u[k] = Kp

⋅ e[k] + Ki

⋅ I[k] + Kd

⋅ D[k]

### 4.2.2. Giới hạn đầu ra

Tín hiệu điều khiển của mỗi trục được giới hạn trong một khoảng xác định nhằm

tránh yêu cầu góc nghiêng vượt quá khả năng cơ khí và đảm bảo tính ổn định của hệ

thống. Các giá trị điều khiển này được diễn giải như độ dốc của mặt phẳng theo hai trục

x và y.

Theo thiết kế này, các giá trị ux
và uy

được ràng buộc trong khoảng [−0.25, 0.25].

### 4.3. Tính góc nghiêng thông qua động học ngược

Tín hiệu điều khiển từ bộ PID (ux
, uy

) được sử dụng để xác định góc nghiêng

mong muốn của mặt phẳng, bao gồm độ nghiêng và độ cao tham chiếu ℎz
. Nhiệm vụ
của khối động học nghịch là ánh xạ từ tư thế này sang các góc quay (hoặc vị trí tương

đương) của từng cơ cấu chấp hành, sao cho mặt phẳng đạt được trạng thái mong muốn.

### 4.3.1. Biểu diễn độ nghiêng bằng vector pháp tuyến

Độ nghiêng của mặt phẳng được biểu diễn thông qua vector pháp tuyến chưa chuẩn

hoá:

n = (nx
, ny

, 1)

trong đó (nx
, ny

) được suy ra trực tiếp từ tín hiệu điều khiển (ux , uy

) và giả thiết nz >

0. Vector này sau đó được chuẩn hoá:

n̂ =

n
‖n‖

Cách biểu diễn này phù hợp trong miền góc nghiêng nhỏ, khi (nx , ny

) có thể được xem

như xấp xỉ độ dốc (gradient) của mặt phẳng.

### 4.3.2. Tách bài toán theo từng chân

Hệ thống gồm ba cơ cấu chấp hành được bố trí lệch nhau 120°. Để tính toán độc

lập cho từng chân, vector (nx
, ny

) được biến đổi sang hệ trục cục bộ của từng cơ cấu

thông qua phép quay phẳng:

rx = nx

cos α − ny

sin α

ry = nx

sin α + ny

cos α

trong đó α là góc định hướng của từng chân.

Từ các thành phần này, vị trí tương đối của khớp cầu (ví dụ các tọa độ joint_y,

joint_z) được xác định dựa trên mô hình hình học của cơ cấu.

### 4.3.3. Tính góc tay đòn

Từ các tọa độ hình học (joint_y, joint_z), độ dài tương đương được xác định:

mag = √joint²
y + joint²
z

Để đảm bảo ổn định số, trường hợp mag tiến gần về 0 được loại bỏ nhằm tránh phép

chia không xác định.

Dựa trên các tham số hình học đã định nghĩa trước, các tỉ số trung gian được xác

định:

ratio1 =

jointy
mag

, ratio2 =

mag² + (L

2
a − L

2
r

)
2La

⋅ mag

trong đó:
- La

là chiều dài tay đòn (ARM_LENGTH)

- Lr

là chiều dài thanh nối (ROD_LENGTH)

Các tỉ số này được ràng buộc trong miền [−1, 1] để đảm bảo tính hợp lệ của hàm lượng

giác ngược. Từ đó, góc quay của tay đòn sau đó được xác định:

θ° = arccos(ratio1

) + arccos(ratio2

)

### 4.4. Cập nhật toạ độ điều khiển cho cơ cấu chấp hành

Từ các giá trị góc θ tính được từ khối động học nghịch, hệ thống xác định vị trí mục

tiêu mới cho từng động cơ bước:

ptarget = θorigin − θ

trong đó:
- θorigin là góc gốc của cơ cấu chấp hành khi mặt phẳng nằm ngang (thực nghiệm

cho kết quả khoảng 300°).

Để đảm bảo cơ cấu chấp hành đạt vị trí mục tiêu trong một chu kỳ điều khiển, vận tốc

được tính dựa trên khoảng cách giữa vị trí hiện tại và vị trí mục tiêu:

v =

|ptarget − pcurrent|
N

trong đó:
- pcurrent là vị trí hiện tại của động cơ,
- N là số chu kỳ tạo xung của động cơ bước trong một chu kỳ điều khiển chính.

Trong thiết kế này, bộ điều khiển chính hoạt động ở tần số 200Hz, trong khi bộ tạo xung

cho cơ cấu chấp hành hoạt động ở tần số 40kHz, tương ứng với:

N =

40kHz
200Hz

= 200

Các giá trị vị trí mục tiêu và vận tốc sau đó được cập nhật vào bộ điều khiển động cơ

bước để thực hiện nội suy chuyển động liên tục giữa các chu kỳ điều khiển.

### 4.5. Điều khiển cơ cấu chấp hành

Sau khi tính được góc nghiêng mong muốn, dựa trên lý thuyết tại Mục 2.3, hệ thống

chuyển đổi sang vị trí mục tiêu của từng động cơ bước. Việc phát xung STEP và xác

định chiều quay DIR được thực hiện trong ngắt timer tần số 40kHz nhằm đảm bảo tín

hiệu điều khiển ổn định và đáp ứng yêu cầu thời gian thực.

Hệ thống sử dụng chế độ vi bước 1/16, tương ứng với độ phân giải dịch chuyển nhỏ

hơn 0.1 mm tại đầu ra cơ cấu chấp hành, giúp tăng độ mượt và độ chính xác khi điều

khiển mặt phẳng.

Đối với mỗi động cơ, hệ thống lưu trữ vị trí hiện tại và vị trí mục tiêu. Từ sai lệch vị

trí, một giá trị vận tốc được tính toán và giới hạn trong phạm vi cho phép để tránh vượt

quá tần số phát xung tối đa. Trong mỗi chu kỳ timer, giá trị vận tốc được cộng vào một

biến tích lũy. Khi giá trị tích lũy đạt ngưỡng 1, hệ thống phát một xung STEP, cập nhật

tín hiệu DIR tương ứng và thay đổi vị trí hiện tại của động cơ.

Khi động cơ đạt vị trí mục tiêu, quá trình tích lũy được dừng và không phát thêm xung điều khiển. Phương pháp này cho phép điều khiển vận tốc dưới dạng số thực, tạo

chuyển động mượt mà trong khi vẫn duy trì độ chính xác vị trí và tính ổn định của

hệ thống.

## CHƯƠNG 5: KIỂM THỬ VÀ ĐÁNH GIÁ

### 5.1. Thiết lập thử nghiệm

Để hỗ trợ quá trình kiểm thử và hiệu chỉnh PID, một công cụ thu thập dữ liệu thời

gian thực được xây dựng bằng giao tiếp UART. Dữ liệu từ vi điều khiển được truyền qua

bộ chuyển đổi USB-to-TTL đến máy tính.

Thư viện pyserial được sử dụng để đọc dữ liệu được gửi từ vi điều khiển, cho

phép thu thập thông tin về vị trí hiện tại của quả bóng, vị trí mục tiêu và tín hiệu điều

khiển trong thời gian thực.

Thư viện matplotlib được sử dụng để trực quan hóa dữ liệu dưới dạng đồ thị, giúp

đánh giá đáp ứng của hệ thống và hỗ trợ quá trình tối ưu tham số điều khiển.

### 5.2. Kết quả, phân tích và đánh giá

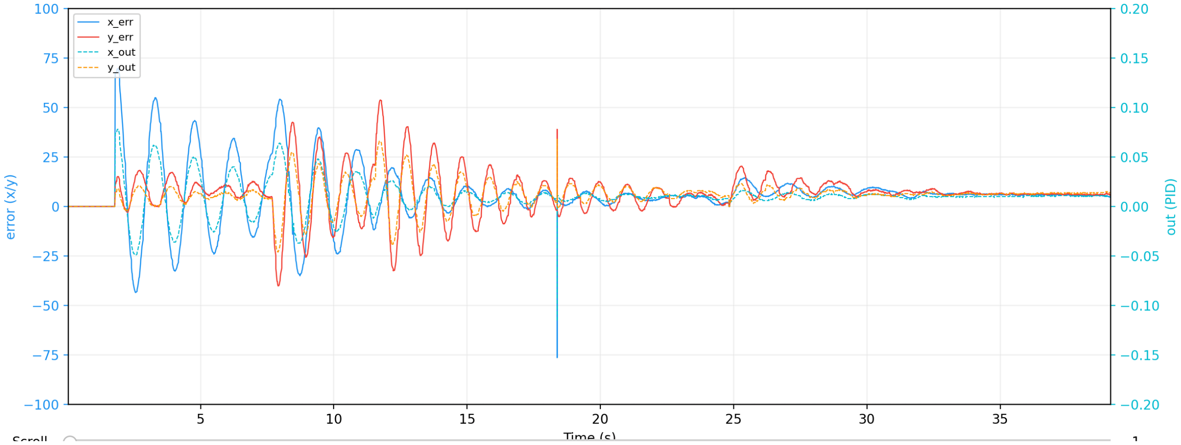
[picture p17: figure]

Hình 5.1: Đồ thị biểu diễn sự thay đổi về đầu vào/ra của hai trục X/Y

(09/06/2026 - 16:38:50)

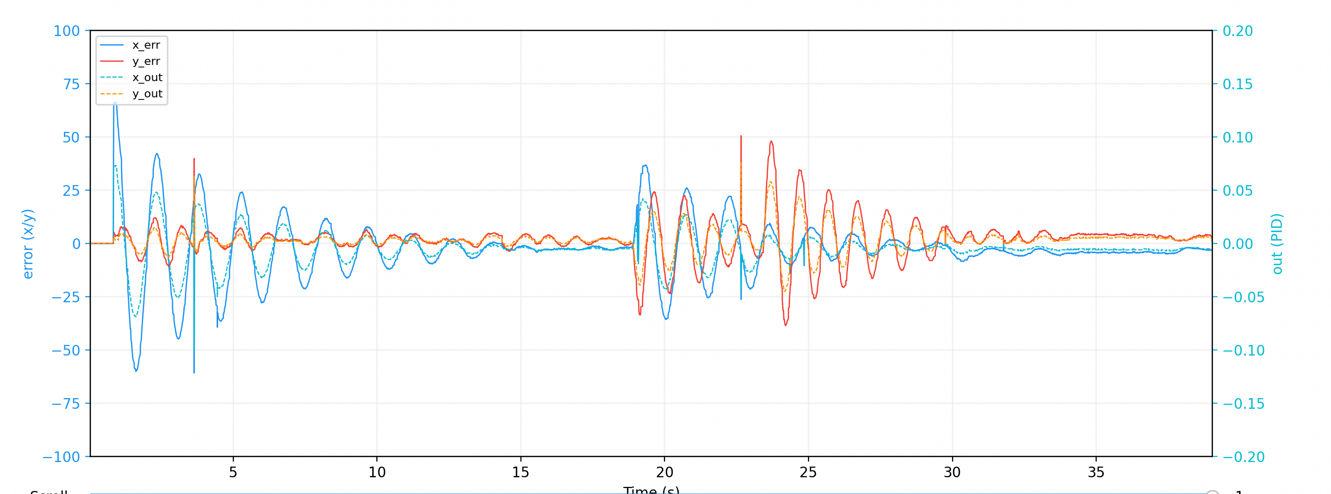
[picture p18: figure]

Hình 5.2: Đồ thị biểu diễn sự thay đổi về đầu vào/ra của hai trục X/Y

(09/06/2026 - 16:58:05)

Bảng 5.1: Thống kê đặc tính của hệ thống

Đặc tính | Trục X | Trục Y
Sai số cực đại | 82.761 mm | 28.786 mm
Sai số cực tiểu | −78.366 mm | −20.643 mm
Biên độ xuất lực Max | 0.078 | 0.030
Sai số xác lập trung bình | 2.138 mm | 2.937 mm
Độ lệch chuẩn pha cuối | 2.506 mm | 2.498 mm
Thời gian xác lập | 29.3 s | 35.6 s

Từ các số liệu trên, có thể rút ra một số nhận xét đặc tính của hệ thống như sau:

a) Sai số xác lập: Hệ thống đạt được sai số xác lập trung bình lần lượt là 2.138 mm

(trục X) và 2.937 mm (trục Y), Kết quả này cho thấy bộ điều khiển có khả năng đưa quả

bóng về gần vị trí mục tiêu, tuy nhiên sai số vẫn chưa được triệt tiêu hoàn toàn.

b) Tính đối xứng giữa hai trục: Độ lệch chuẩn ở trạng thái xác lập của hai trục

gần như tương đương nhau (2.506 mm và 2.498 mm), cho thấy đáp ứng của hệ thống

tương đối đồng nhất trên cả hai phương chuyển động.

c) Khả năng hiệu chỉnh sai lệch lớn: Các giá trị sai số cực đại và cực tiểu cho

thấy hệ thống có khả năng đưa quả bóng trở lại vùng cân bằng ngay cả khi xuất hiện sai

lệch vị trí tương đối lớn. Điều này thể hiện tính ổn định và khả năng phục hồi của bộ

điều khiển. Tuy nhiên ở vùng biên có thể xuất hiện hiện tượng không ổn định hoặc dao

động lớn.

d) Thời gian xác lập: Hệ thống đạt trạng thái ổn định sau khoảng 29.3 s (trục X)

và 35.6 s (trục Y). Mặc dù hệ thống có khả năng hội tụ ổn định, thời gian xác lập vẫn

còn tương đối lớn, đặc biệt trên trục Y.

e) Dao động tại trạng thái xác lập: Sau khi kết thúc giai đoạn quá độ, hệ thống

vẫn tồn tại dao động rất nhỏ quanh vị trí cân bằng.

## CHƯƠNG 6: KẾT LUẬN

Trong quá trình thực hiện đề tài, nhóm đã nghiên cứu và xây dựng thành công hệ

thống cân bằng bóng đáp ứng được tương đối mục tiêu và phạm vi ban đầu. Các kết quả

thực nghiệm cho thấy bộ điều khiển hoạt động ổn định, đáp ứng tương đối nhanh và có

khả năng giảm sai số hiệu quả.

Tuy vậy, hệ thống vẫn còn tồn tại hạn chế, như độ chính xác chưa cao, thiết kế cơ

khí còn đơn giản, thời gian xác lập chưa đạt mức lý tưởng, và khả năng ứng dụng thực tế còn hạn chế. Những hạn chế này mở ra nhiều hướng phát triển tiềm năng để cải thiện

hiệu năng và tính ứng dụng của hệ thống trong tương lai. Một số hướng phát triển có thể

được xem xét bao gồm:

- Sử dụng hệ thống cảm biến chính xác và hỗ trợ đa dạng hơn (ví dụ xử lý ảnh) để

thay thế cho màn cảm ứng điện trở.

- Tối ưu thêm các tham số của bộ điều khiển PID hoặc áp dụng các phương pháp

điều khiển hiện đại hơn như LQR hoặc học máy nhằm cải thiện độ ổn định và

chất lượng đáp ứng.

- Cải tiến cơ cấu chấp hành để giảm độ trễ cơ học và tăng độ chính xác trong quá

trình điều khiển góc nghiêng của mặt phẳng.

- Mở rộng hệ thống để xử lý các bài toán phức tạp hơn, chẳng hạn như cân bằng

nhiều quả bóng đồng thời hoặc hoạt động trên các bề mặt có hình dạng khác nhau.

## Tài liệu tham khảo

[1] Aaed Musa, “Ball Balancer,” Apr. 2023. [Online]. Available: https://www.

instructables.com/Ball-Balancer/

[2] Khaled Magdy, “STM32 RCC Clock Configuration – Ultimate Guide.” [Online].

Available: https://deepbluembedded.com/stm32-rcc-clock-configuration-ultimate-

guide/ (https://deepbluembedded.com/stm32-rcc-clock-configuration-ultimate-guide/)

[3] Khaled Magdy, “STM32 delay_us Microseconds (STM32 DWT & Timer
Delay).” | [Online]. | Available: | https://deepbluembedded.com/stm32-delay-

microsecond-millisecond-utility-dwt-delay-timer-delay/ (https://deepbluembedded.com/stm32-delay-microsecond-millisecond-utility-dwt-delay-timer-delay/)

[4] Khaled Magdy, “STM32 ADC DMA Example HAL+ Interrupt, Polling (Single

Channel).” [Online]. Available: https://deepbluembedded.com/stm32-adc-read-

example-dma-interrupt-polling/ (https://deepbluembedded.com/stm32-adc-read-example-dma-interrupt-polling/)

[5] Khaled Magdy, “STM32 GPIO Registers (Direct Register Access) Fast Pin

Control.” [Online]. Available: https://deepbluembedded.com/stm32-gpio-registers-

direct-access-fast-pin-control/ (https://deepbluembedded.com/stm32-gpio-registers-direct-access-fast-pin-control/)

[6] Khaled Magdy, “STM32 Timer Interrupt HAL Example – Timer Mode

LAB.” [Online]. Available: https://deepbluembedded.com/stm32-timer-interrupt-

hal-example-timer-mode-lab/ (https://deepbluembedded.com/stm32-timer-interrupt-hal-example-timer-mode-lab/)

## Phụ lục

Mã nguồn của hệ thống tại: https://github.com/justmangoou/ball-balancer

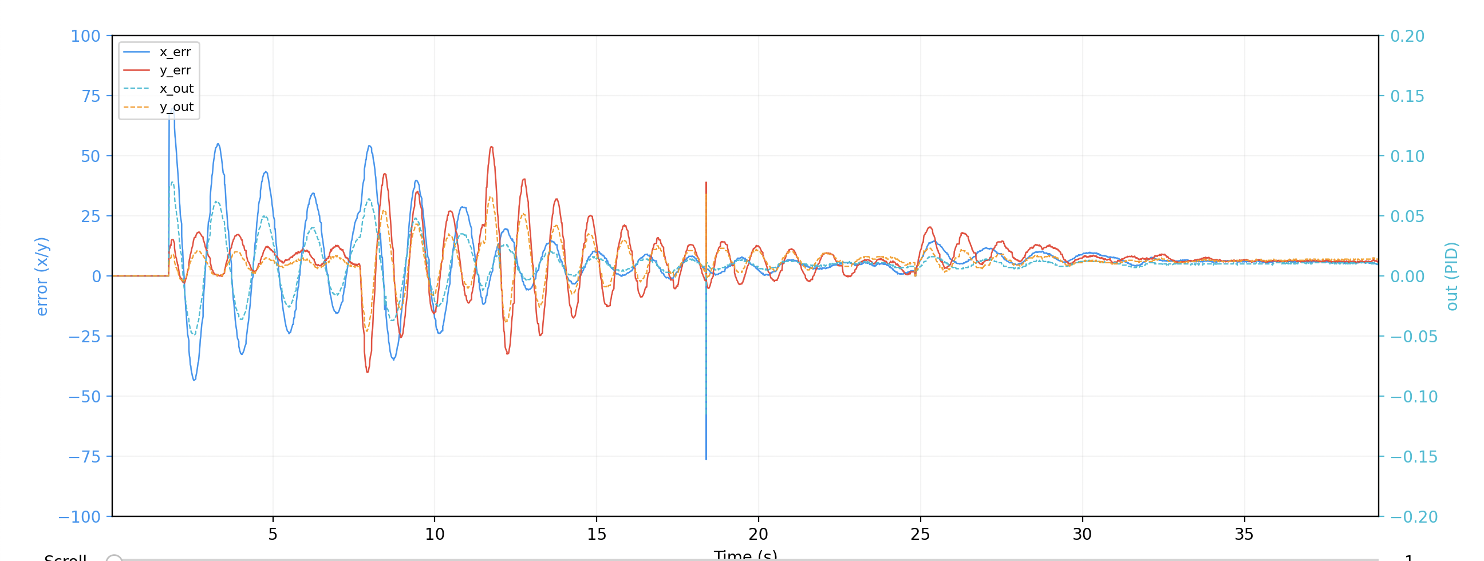
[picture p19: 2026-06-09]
report/assets/graph_data_1.png

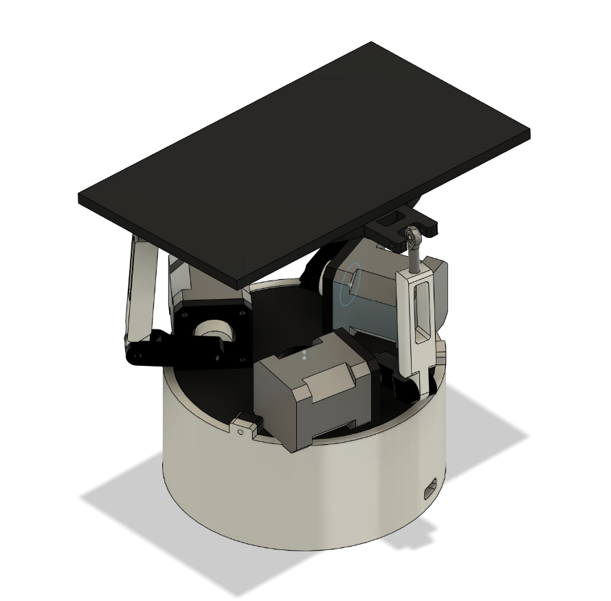
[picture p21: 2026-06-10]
report/assets/3d-design.png

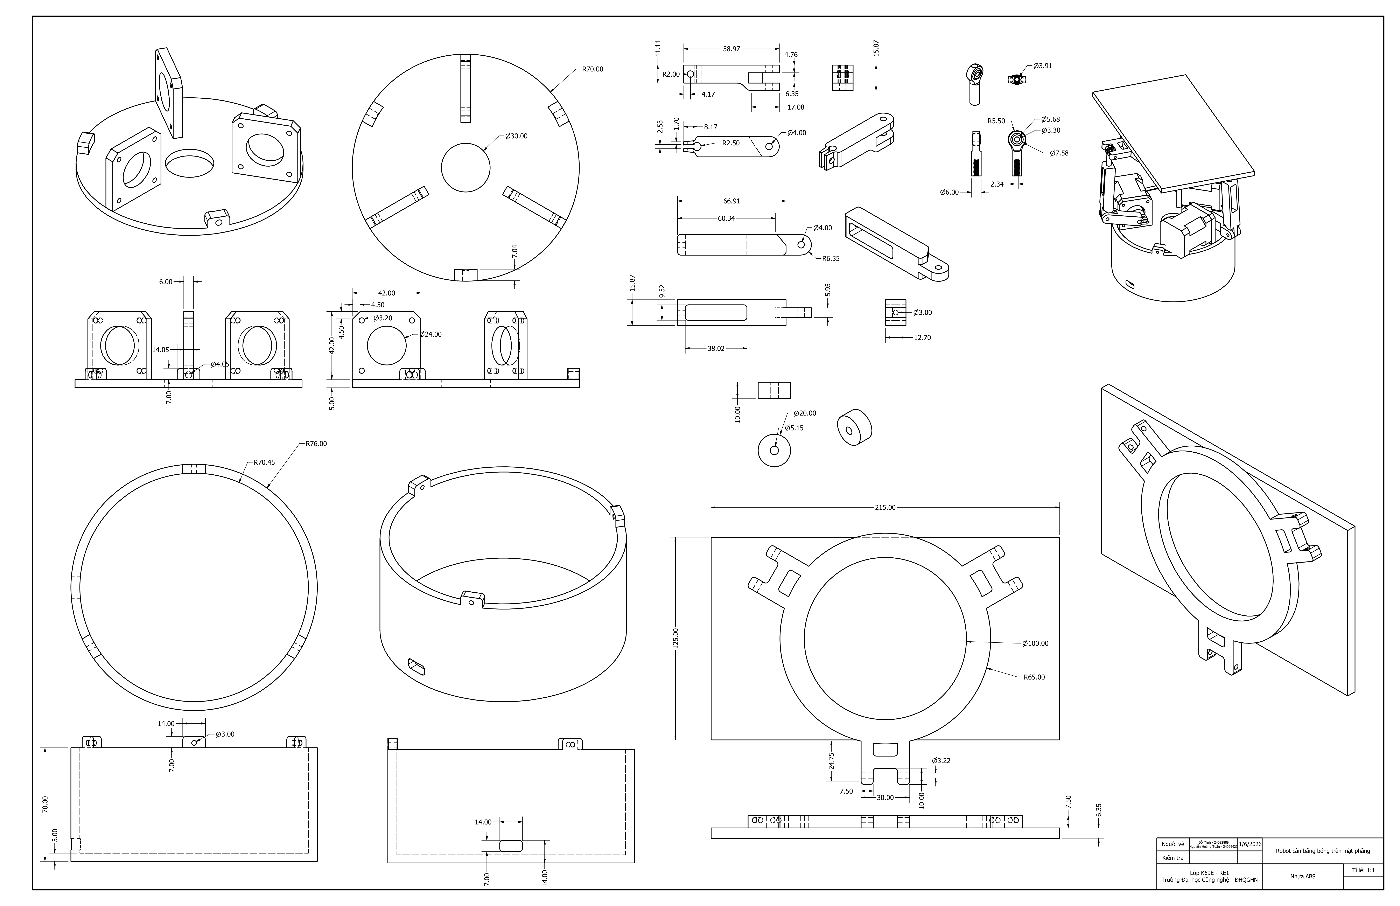
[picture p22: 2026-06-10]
report/assets/technical-drawing.png

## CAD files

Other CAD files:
CAD files/59935K13_Ball Joint Rod End.ipt
CAD files/Stepper 42 v1.ipt
CAD files/base plate v3.ipt
CAD files/base platform final v2.ipt
CAD files/base stand v2 v2.idw
CAD files/base stand v2 v2.ipt
CAD files/link_#1+(x3) v6.ipt
CAD files/link_#2+(x3) v1.ipt
CAD files/mo phong.iam
CAD files/spacer v4.ipt

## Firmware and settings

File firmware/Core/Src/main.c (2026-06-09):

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
/* Includes ------------------------------------------------------------------*/
#include "main.h"

/* USER CODE BEGIN Includes */
#include <stdio.h>

#include "controller.h"
#include "resistive_touch.h"
#include "stepper_driver.h"
/* USER CODE END Includes */

/* USER CODE BEGIN PD */
#define PUTCHAR_PROTOTYPE int __io_putchar(int ch)
/* USER CODE END PD */

ADC_HandleTypeDef hadc1;

TIM_HandleTypeDef htim5;
TIM_HandleTypeDef htim9;

UART_HandleTypeDef huart1;

/* USER CODE BEGIN PV */
static uint32_t hclk_mhz;
static uint32_t last_tick;

#ifndef NDEBUG
volatile uint16_t x_raw, y_raw;
volatile float x_pos, y_pos;
volatile uint16_t pressure;

volatile float x_out, y_out;
volatile float a_theta, b_theta, c_theta;
#endif

volatile bool err_occurred = false;
/* USER CODE END PV */

void SystemClock_Config(void);
static void MX_GPIO_Init(void);
static void MX_ADC1_Init(void);
static void MX_TIM5_Init(void);
static void MX_TIM9_Init(void);
static void MX_USART1_UART_Init(void);
/* USER CODE BEGIN PFP */
static void DWT_Init(void);
/* USER CODE END PFP */

/**
  * @brief  The application entry point.
  * @retval int
  */
int main(void)
{

  /* MCU Configuration--------------------------------------------------------*/

  /* Reset of all peripherals, Initializes the Flash interface and the Systick. */
  HAL_Init();

  /* USER CODE BEGIN Init */
  #if !defined(__FPU_USED) || (__FPU_USED != 1)
  #error "FPU is NOT enabled in the compiler! Check CMake flags."
  #endif

  SCB->CPACR |= ((3UL << 10*2) | (3UL << 11*2));
  /* USER CODE END Init */

  /* Configure the system clock */
  SystemClock_Config();

  /* USER CODE BEGIN SysInit */
  DWT_Init();
  /* USER CODE END SysInit */

  /* Initialize all configured peripherals */
  MX_GPIO_Init();
  MX_ADC1_Init();
  MX_TIM5_Init();
  MX_TIM9_Init();
  MX_USART1_UART_Init();
  /* USER CODE BEGIN 2 */
  Touch_Init();
  Controller_Init();

  HAL_TIM_Base_Start_IT(&htim5);
  HAL_TIM_Base_Start_IT(&htim9);
  /* USER CODE END 2 */

  /* Infinite loop */
  /* USER CODE BEGIN WHILE */
  setvbuf(stdout, NULL, _IONBF, 0);
  while (1)
  {
    /* USER CODE END WHILE */

    /* USER CODE BEGIN 3 */
    const float x_err = 0 - x_pos, y_err = 0 - y_pos;
    //printf("x_raw: %d | y_raw: %d | z: %d | x_pos: %.2f | y_pos: %.2f \n", x_raw, y_raw, pressure, x_pos, y_pos);
    printf("x_err: %.3f | y_err: %.3f | x_out: %.3f | y_out: %.3f | a_theta: %.3f | b_theta: %.3f | c_theta: %.3f \n", x_err, y_err, x_out, y_out, a_theta, b_theta, c_theta);
  }
  /* USER CODE END 3 */
}

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
/* USER CODE BEGIN 4 */
PUTCHAR_PROTOTYPE
{
  /* Place your implementation of fputc here */
  /* e.g. write a character to the USART1 and Loop until the end of transmission */
  HAL_UART_Transmit(&huart1, (uint8_t *)&ch, 1, 0xFFFF);

  return ch;
}

void DWT_Init(void) {
  SystemCoreClockUpdate();
  hclk_mhz = HAL_RCC_GetHCLKFreq() / 1000000;

  // Force enablement directly
  CoreDebug->DEMCR |= CoreDebug_DEMCR_TRCENA_Msk;
  DWT->CYCCNT = 0;
  DWT->CTRL |= DWT_CTRL_CYCCNTENA_Msk;

  last_tick = DWT->CYCCNT;
}

void DWT_Delay_us(const uint32_t microseconds)
{
  const uint32_t start_tick = DWT->CYCCNT;
  const uint32_t delay_cycles = microseconds * hclk_mhz;
  while ((DWT->CYCCNT - start_tick) < delay_cycles);
}

uint32_t ADC_Read_Polling(const uint32_t timeout)
{
  uint32_t result = 0;

  if (HAL_ADC_PollForConversion(&hadc1, timeout) == HAL_OK) {
    result = HAL_ADC_GetValue(&hadc1);
  }

  return result;
}

void GPIO_SetPinMode(GPIO_TypeDef* port, const uint16_t pin, const uint32_t mode, const uint32_t pull)
{
#if FAST_GPIO_SET_PIN
  // From https://deepbluembedded.com/stm32-gpio-registers-direct-access-fast-pin-control/
  // Get pin index (0 to 15) from bitmask
  const uint32_t pin_pos = __builtin_ctz(pin);
  const uint32_t bit_offset = pin_pos * 2;

  // Update MODER (Mode Register)
  // Clear 2 bits, then set new mode. HAL constants for
  // INPUT (0), OUTPUT (1), and ANALOG (3) match register values.
  port->MODER = (port->MODER & ~(0x3U << bit_offset)) | ((mode & 0x3U) << bit_offset);

  // Update PUPDR (Pull-up/Pull-down Register)
  port->PUPDR = (port->PUPDR & ~(0x3U << bit_offset)) | (pull << bit_offset);
#else
  GPIO_InitTypeDef GPIO_InitStruct = {0};
  GPIO_InitStruct.Pin = pin;
  GPIO_InitStruct.Mode = mode;
  GPIO_InitStruct.Pull = pull;
  GPIO_InitStruct.Speed = GPIO_SPEED_FREQ_VERY_HIGH;
  HAL_GPIO_Init(port, &GPIO_InitStruct);
#endif
}
/* USER CODE END 4 */
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


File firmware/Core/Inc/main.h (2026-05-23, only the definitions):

#define LED_Pin GPIO_PIN_13
#define LED_GPIO_Port GPIOC
#define TOUCH_X_POS_Pin GPIO_PIN_1
#define TOUCH_X_POS_GPIO_Port GPIOA
#define TOUCH_Y_POS_Pin GPIO_PIN_2
#define TOUCH_Y_POS_GPIO_Port GPIOA
#define TOUCH_X_NEG_Pin GPIO_PIN_3
#define TOUCH_X_NEG_GPIO_Port GPIOA
#define TOUCH_Y_NEG_Pin GPIO_PIN_4
#define TOUCH_Y_NEG_GPIO_Port GPIOA
#define LEG_ENABLE_Pin GPIO_PIN_12
#define LEG_ENABLE_GPIO_Port GPIOB
#define LEG_A_DIR_Pin GPIO_PIN_15
#define LEG_A_DIR_GPIO_Port GPIOA
#define LEG_A_STEP_Pin GPIO_PIN_3
#define LEG_A_STEP_GPIO_Port GPIOB
#define LEG_B_DIR_Pin GPIO_PIN_4
#define LEG_B_DIR_GPIO_Port GPIOB
#define LEG_B_STEP_Pin GPIO_PIN_5
#define LEG_B_STEP_GPIO_Port GPIOB
#define LEG_C_DIR_Pin GPIO_PIN_6
#define LEG_C_DIR_GPIO_Port GPIOB
#define LEG_C_STEP_Pin GPIO_PIN_7
#define LEG_C_STEP_GPIO_Port GPIOB
#define MISS_THRESHOLD 20
#define FAST_GPIO_SET_PIN    true
#define DEFAULT_ADC_POLLING_TIMEOUT 10
#define LEG_A_TIM            TIM2
#define LEG_A_TIM_CHANNEL    TIM_CHANNEL_2
#define LEG_B_TIM            TIM3
#define LEG_B_TIM_CHANNEL    TIM_CHANNEL_2
#define LEG_C_TIM            TIM4
#define LEG_C_TIM_CHANNEL    TIM_CHANNEL_2
#define HEARTBEAT_TIM        TIM5
#define HEARTBEAT_DELTA_TIME 0.005f

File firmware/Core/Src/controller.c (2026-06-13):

#include "controller.h"

#include <stdint.h>
#include <stdlib.h>
#include "resistive_touch.h"
#include "main.h"
#include "math_extra.h"

static PID_Controller X_CONTROLLER = {1.1E-3f, 7.5E-5f, 2.3E-5f};
static PID_Controller Y_CONTROLLER = {1.1E-3f, 7.5E-5f, 2.3E-5f};
Stepper* LEG_STEPPER_CONTROLLER[3] = { NULL };

extern TIM_HandleTypeDef htim2;
extern TIM_HandleTypeDef htim3;
extern TIM_HandleTypeDef htim4;
extern float x_out, y_out;
extern float a_theta, b_theta, c_theta;

static bool is_first_update = true;
volatile float times;

static void prv_move(float nx, float ny);
static float prv_pid_compute(PID_Controller *pid, float setpoint, float measured, float dt);
static void prv_pid_reset(PID_Controller *pid);
static float prv_theta_compute(Leg leg, float hz, float nx, float ny);

void Controller_Init(void) {
  LEG_STEPPER_CONTROLLER[LEG_A] = Stepper_New(LEG_A_STEP_GPIO_Port, LEG_A_STEP_Pin, LEG_A_DIR_GPIO_Port, LEG_A_DIR_Pin);
  LEG_STEPPER_CONTROLLER[LEG_B] = Stepper_New(LEG_B_STEP_GPIO_Port, LEG_B_STEP_Pin, LEG_B_DIR_GPIO_Port, LEG_B_DIR_Pin);
  LEG_STEPPER_CONTROLLER[LEG_C] = Stepper_New(LEG_C_STEP_GPIO_Port, LEG_C_STEP_Pin, LEG_C_DIR_GPIO_Port, LEG_C_DIR_Pin);

  if (LEG_STEPPER_CONTROLLER[LEG_A] == NULL ||
      LEG_STEPPER_CONTROLLER[LEG_B] == NULL ||
      LEG_STEPPER_CONTROLLER[LEG_C] == NULL
  ) {
    Error_Handler();
  }

  Stepper_Enable();
  Controller_Reset();
}

void Controller_Test(void) {
  Stepper_MoveTo(LEG_STEPPER_CONTROLLER[LEG_B], LEG_STEPPER_CONTROLLER[LEG_B]->current_pos + 50, 0.025f);
}

void Controller_Update(Touch_CenterOffsetPercentage *offset) {
  if (is_first_update) {
    X_CONTROLLER.prev_error = 0.0f - offset->x;
    Y_CONTROLLER.prev_error = 0.0f - offset->y;
    is_first_update = false;
  }

  x_out = prv_pid_compute(&X_CONTROLLER, 0, offset->x, HEARTBEAT_DELTA_TIME);
  y_out = prv_pid_compute(&Y_CONTROLLER, 0, offset->y, HEARTBEAT_DELTA_TIME);

  x_out = clampf(x_out, -0.2f, 0.2f);
  y_out = clampf(y_out, -0.2f, 0.2f);

  prv_move(x_out, y_out);
}

void Controller_Reset(void) {
  prv_pid_reset(&X_CONTROLLER);
  prv_pid_reset(&Y_CONTROLLER);
  is_first_update = true;

  x_out = 0.0f;
  y_out = 0.0f;

  prv_move(0, 0);
}

static void prv_move(const float ux, const float uy) {
  const float nx = uy;
  const float ny = -ux;

  for (uint8_t i = 0; i < LEG_COUNT; i++) {
    Stepper *s = LEG_STEPPER_CONTROLLER[i];

    const float theta = prv_theta_compute(i, 51.3f, nx, ny);
    const int32_t new_target = lroundf((ORIGIN_ANGLE - theta) * ANGLE_TO_STEP);

    if (i == 0) {
      a_theta = theta;
    } else if (i == 1) {
      b_theta = theta;
    } else if (i == 2) {
      c_theta = theta;
    }

    /* VELOCITY CALCULATION (Bresenham/Accumulator)
       We want to reach the new target within 1 Heartbeat (5ms).
       If Muscle Timer is 40kHz, we have 200 ticks per Heartbeat.
       Velocity = Distance / Ticks
    */
    const float dist = (float)abs(new_target - s->current_pos);
    const float velocity = dist / 200.0f;

    Stepper_MoveTo(s, new_target, velocity);
  }
}

static float prv_pid_compute(PID_Controller *pid, const float setpoint, const float measured, const float dt) {
  const float error = setpoint - measured;
  const float kp = pid->kp;
  const float ki = pid->ki;
  const float kd = pid->kd;

  pid->integral += (error + pid->prev_error) * 0.5f * dt;
  const float max_i = 0.036f / (ki > 0 ? ki : 1.0f);
  pid->integral = clampf(pid->integral, -max_i, max_i);

  const float raw_derivative = (error - pid->prev_error) / dt;
  pid->filtered_d = (0.1f * raw_derivative) + (0.9f * pid->filtered_d);
  const float output = (kp * error) + (ki * pid->integral) + (kd * pid->filtered_d);

  pid->prev_error = error;

  return output;
}

static void prv_pid_reset(PID_Controller *pid) {
  pid->integral = 0;
  pid->prev_error = 0;
}

/**
 * @brief Computes the inverse kinematics for a single leg of a 3-motor platform.
 * * Calculates the required motor angle (theta) to achieve a specific platform
 * height and tilt. This uses a 2D-projection method by rotating the platform
 * coordinate system to align with the specific leg's axis.
 *
 * @param leg    The leg index (A, B, or C) corresponding to the motor.
 * @param hz     The target center height of the platform in mm.
 * @param nx     The X-component of the platform's normal vector gradient.
 * @param ny     The Y-component of the platform's normal vector gradient.
 * * @return float The calculated motor arm angle in degrees.
 * * @note Assumes a 3-RSS (Revolute-Spherical-Spherical) geometry.
 * @note Optimized for STM32 FPU: Uses lookup tables and minimizes divisions.
 * @warning Returns 0.0f or clamped values if the requested position is
 * physically unreachable (kinematic singularity).
 */
static float prv_theta_compute(const Leg leg, const float hz, const float nx, const float ny) {
  // Normalize vector
  const float nmag = sqrtf(nx * nx + ny * ny + 1.0f);
  const float n_x = nx / nmag;
  const float n_y = ny / nmag;
  const float n_z = 1.0f / nmag;

  const LegInfo *info = &LEGS[leg];

  // Standard 2D rotation for the tilt vector
  const float rx = n_x * info->cos_a - n_y * info->sin_a;
  const float ry = n_x * info->sin_a + n_y * info->cos_a;
  const float rx2 = rx * rx;
  const float ry2 = ry * ry;

  /* Generic Math for a single leg (aligned to Y-axis)
     We use the rotated coordinates (rx, ry) to represent the platform tilt
     relative to the leg's local frame.
  */
  const float nz_p1 = n_z + 1.0f;
  const float inv_nz_p1 = 1.0f / nz_p1;
  const float denom_inv = 1.0f / (nz_p1 - rx2);

  const float term1 = (rx2 + 3.0f * n_z * n_z + 3.0f * n_z) * denom_inv;
  const float term2 = (rx2 * rx2 - 3.0f * rx2 * ry2) * (inv_nz_p1 * inv_nz_p1 * denom_inv);

  const float joint_y = BASE_RADIUS + PLAT_R_HALF * (1.0f - term1 + term2);
  const float joint_z = hz + PLATFORM_RADIUS * ry;

  // Calculate Angle
  const float mag_sq = (joint_y * joint_y) + (joint_z * joint_z);
  const float mag = sqrtf(mag_sq);

  // Make sure mag is not 0 so inv_mag is divisible
  if (mag < 0.0001f) return 0.0f;

  const float inv_mag = 1.0f / mag;

  float ratio_acos1 = joint_y * inv_mag;
  float ratio_acos2 = (mag_sq + ARM_DIFF_SQ) * inv_mag * INV_ARM_L_X2;

  // Arccos/Arcsin input should be in [-1,1]
  ratio_acos1 = clampf(ratio_acos1, -1.0f, 1.0f);
  ratio_acos2 = clampf(ratio_acos2, -1.0f, 1.0f);

  return (acosf(ratio_acos1) + acosf(ratio_acos2)) * RAD_TO_DEG;
}

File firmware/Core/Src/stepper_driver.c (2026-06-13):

#include "stepper_driver.h"

#include <stdlib.h>
#include "math_extra.h"

void Stepper_Enable(void) {
  HAL_GPIO_WritePin(LEG_ENABLE_GPIO_Port, LEG_ENABLE_Pin, GPIO_PIN_RESET);
}

void Stepper_Disable(void) {
  HAL_GPIO_WritePin(LEG_ENABLE_GPIO_Port, LEG_ENABLE_Pin, GPIO_PIN_SET);
}

Stepper *Stepper_New(GPIO_TypeDef *step_port, uint16_t step_pin, GPIO_TypeDef *dir_port, uint16_t dir_pin) {
  Stepper *stepper = malloc(sizeof(Stepper));
  if (stepper == NULL) return NULL;

  stepper->step_port = step_port;
  stepper->step_pin = step_pin;
  stepper->dir_port = dir_port;
  stepper->dir_pin = dir_pin;

  stepper->current_pos = 0;
  stepper->target_pos = 0;
  stepper->current_velocity = 0.0f;
  stepper->target_velocity = 0.0f;
  stepper->accumulator = 0.0f;

  return stepper;
}

void Stepper_MoveTo(Stepper *stepper, const int32_t target_pos, const float velocity) {
  const float max_velocity = STEPPER_MAX_STEP_RATE / STEPPER_TICK_HZ;
  const float clipped_vel = clampf(velocity, 0.0f, max_velocity);

  stepper->target_pos = target_pos;
  stepper->target_velocity = clipped_vel;
}

void Stepper_Process(Stepper *stepper) {
  if (stepper->current_pos == stepper->target_pos) {
    stepper->current_velocity = 0.0f;
    stepper->target_velocity = 0.0f;
    stepper->accumulator = 0.0f;
    return;
  }

  const float error = stepper->target_velocity - stepper->current_velocity;
  const float abs_err = (error > 0.0f) ? error : -error;

  if (abs_err <= STEPPER_ACCEL_RATE) {
    stepper->current_velocity = stepper->target_velocity;
  } else {
    stepper->current_velocity += (error > 0.0f) ? STEPPER_ACCEL_RATE : -STEPPER_ACCEL_RATE;
  }

  stepper->accumulator += stepper->current_velocity;

  while (stepper->accumulator >= 1.0f && stepper->current_pos != stepper->target_pos) {
    stepper->accumulator -= 1.0f;

    if (stepper->target_pos > stepper->current_pos) {
      stepper->dir_port->BSRR = stepper->dir_pin;
      stepper->current_pos++;
    } else {
      stepper->dir_port->BSRR = (uint32_t)stepper->dir_pin << 16;
      stepper->current_pos--;
    }

    DWT_Delay_us(2u);
    stepper->step_port->BSRR = stepper->step_pin;
    DWT_Delay_us(2u);
    stepper->step_port->BSRR = (uint32_t)stepper->step_pin << 16;
    DWT_Delay_us(2u);
  }
}

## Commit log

2026-03-16 fix: add firmware under firmware folder
    [firmware.ioc, main.c, main.h]
2026-04-04 Add resistive touch reader
2026-04-18 chore: add math_extra, tempoary fix resitive touch and controller initial
    [controller.c, controller.h, firmware.ioc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]
2026-04-24 chore: resistive touch
    Fix reading
    Normalize to offset from center
    Heartbeat visualization
    [controller.c, controller.h, firmware.ioc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]
2026-04-28 chore: move to interrupt based instead of using while(1) loop
2026-06-07 chore: calibration
2026-06-08 chore: finalize
    [2026-06-08_10-17-07.csv, 2026-06-08_10-28-15.csv, 2026-06-08_10-33-42.csv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]
2026-06-09 Final tuning and data
    [2026-06-08_10-17-07.csv, 2026-06-08_10-28-15.csv, 2026-06-08_10-33-42.csv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]
2026-06-10 Update report
    [59935K13_Ball Joint Rod End.ipt, Stepper 42 v1.ipt, base plate v3.ipt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]
2026-06-13 chore: new data, add acceleration for stepper motor
    [2026-06-10_20-34-57.csv, 2026-06-13_13-38-00.csv]

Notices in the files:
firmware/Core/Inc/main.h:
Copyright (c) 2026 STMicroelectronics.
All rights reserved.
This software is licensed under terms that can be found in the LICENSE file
